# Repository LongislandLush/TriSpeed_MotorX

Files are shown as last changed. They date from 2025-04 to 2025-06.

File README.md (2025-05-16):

# TriSpeed_MotorX
STM32-based 3-speed DC motor controller with PWM, UART, and state logic

TriSpeed MotorX 是一個基於 STM32 Nucleo-F446RE 開發板的小型馬達控制專案，
實現了按鈕切換三段轉速、OLED即時顯示當前狀態，並透過 UART 通訊將速度資訊同步給 Arduino，控制 RGB LED 顏色變化。





# 系統架構
## STM32 X Arduino X UART X PWM X OLED 系統架構圖
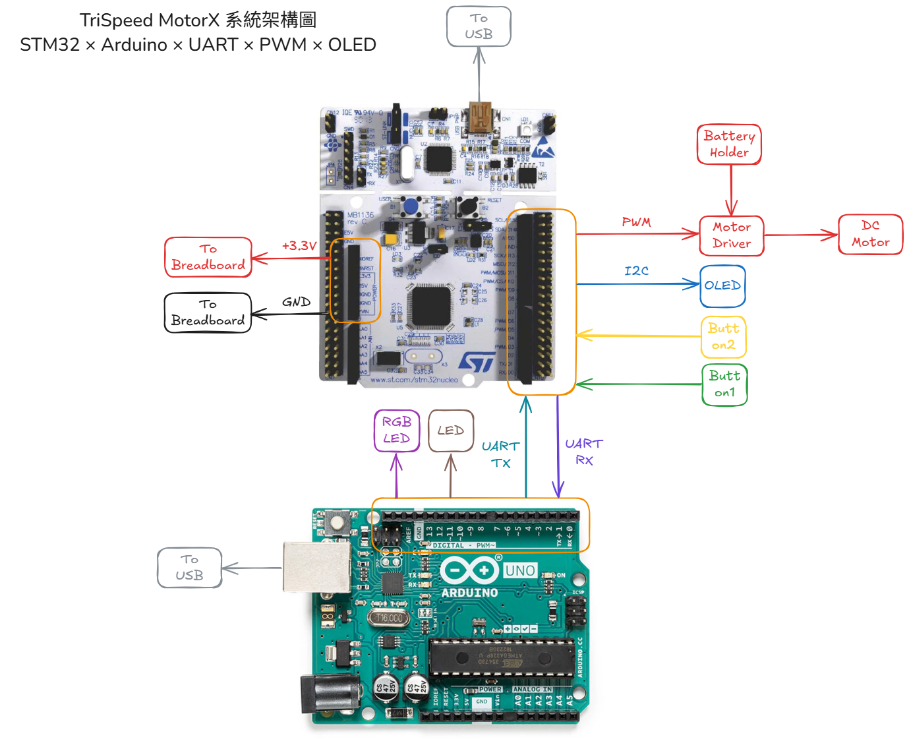
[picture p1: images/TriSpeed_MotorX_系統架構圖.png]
TriSpeed_MotorX_系統架構圖


## Normal Mode 流程圖
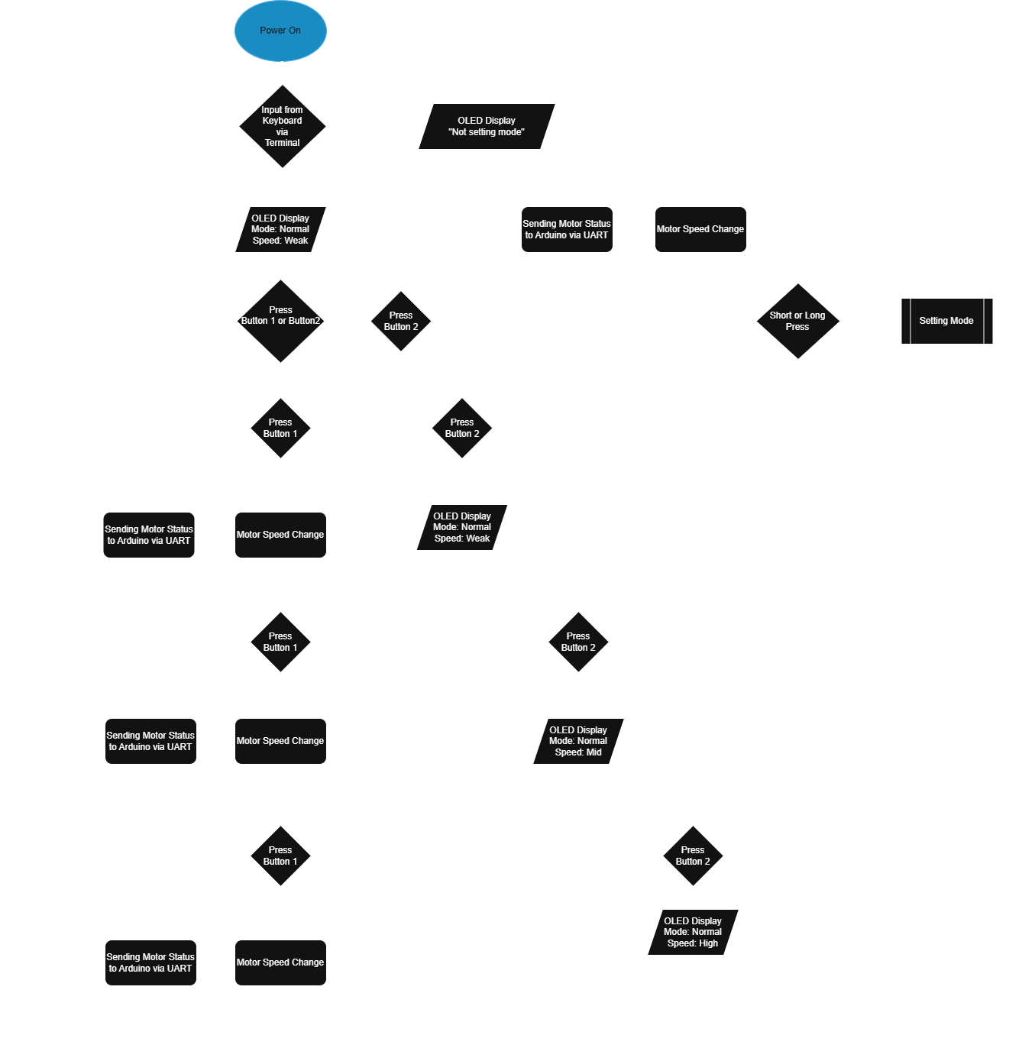
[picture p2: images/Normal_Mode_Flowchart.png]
Normal Mode Flowchart


## Setting Mode 流程圖
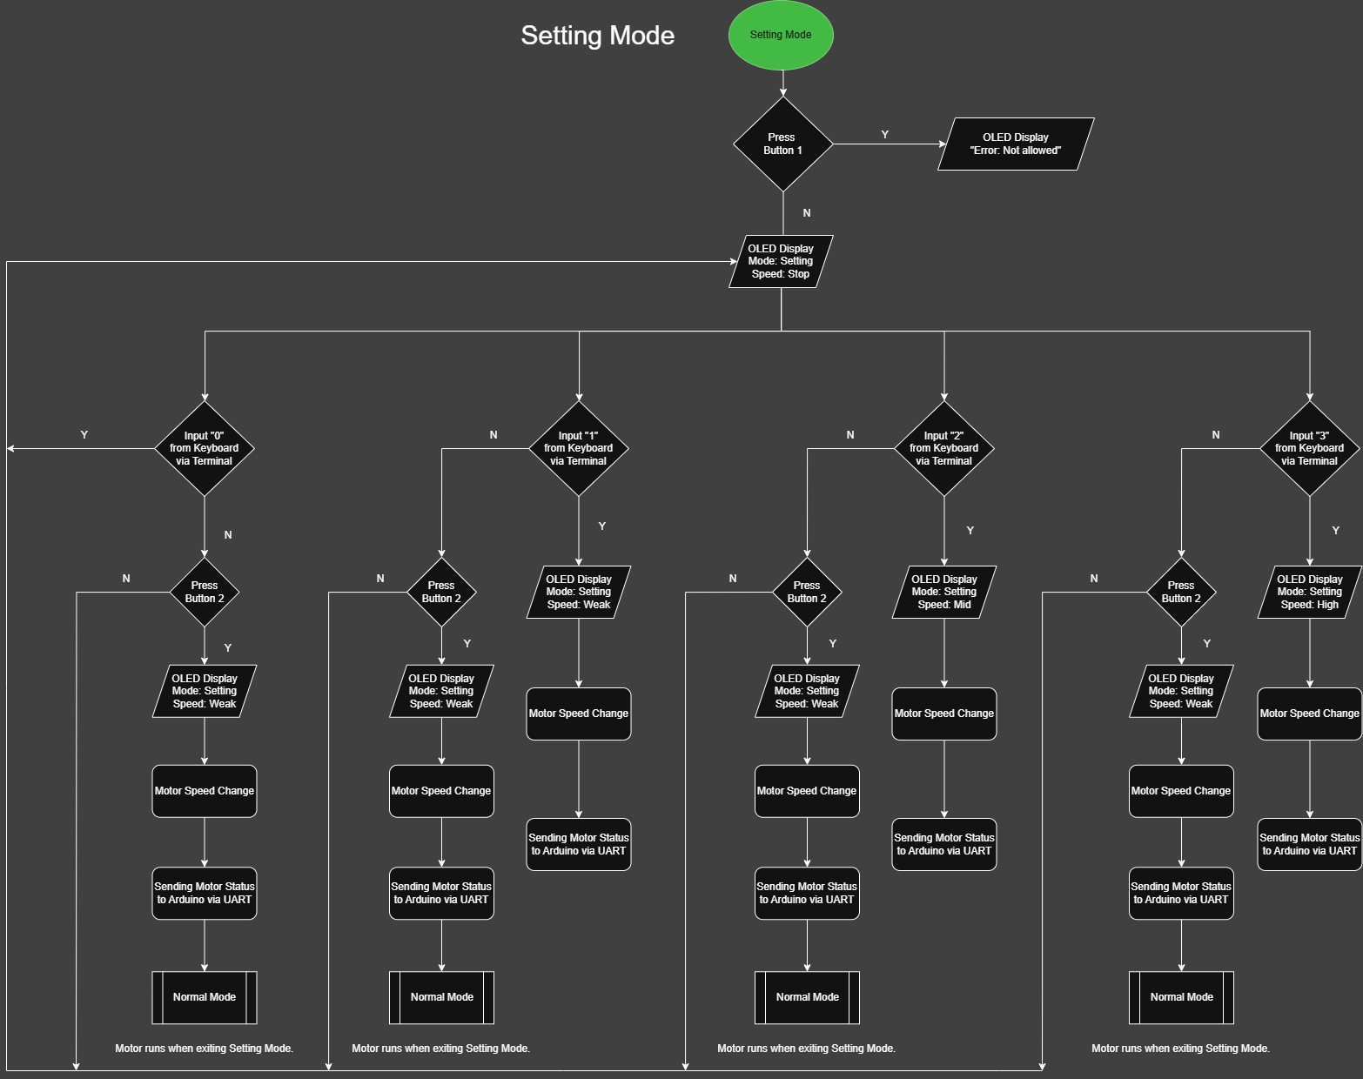
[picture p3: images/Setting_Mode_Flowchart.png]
Setting Mode Flowchart


# 使用方式

環境準備
1. 開啟 STM32CubeIDE
參考 STM32/ 資料夾內的 main.c 與 .ioc 設定，燒錄至 Nucleo-F446RE 開發板。

2. 開啟 Arduino IDE
參考 Arduino/ 資料夾內的 .ino 檔案，燒錄至 Arduino Uno R3。

3. 接線參考
請依據 images/ 資料夾內的接線圖進行連接，特別注意以下幾點：

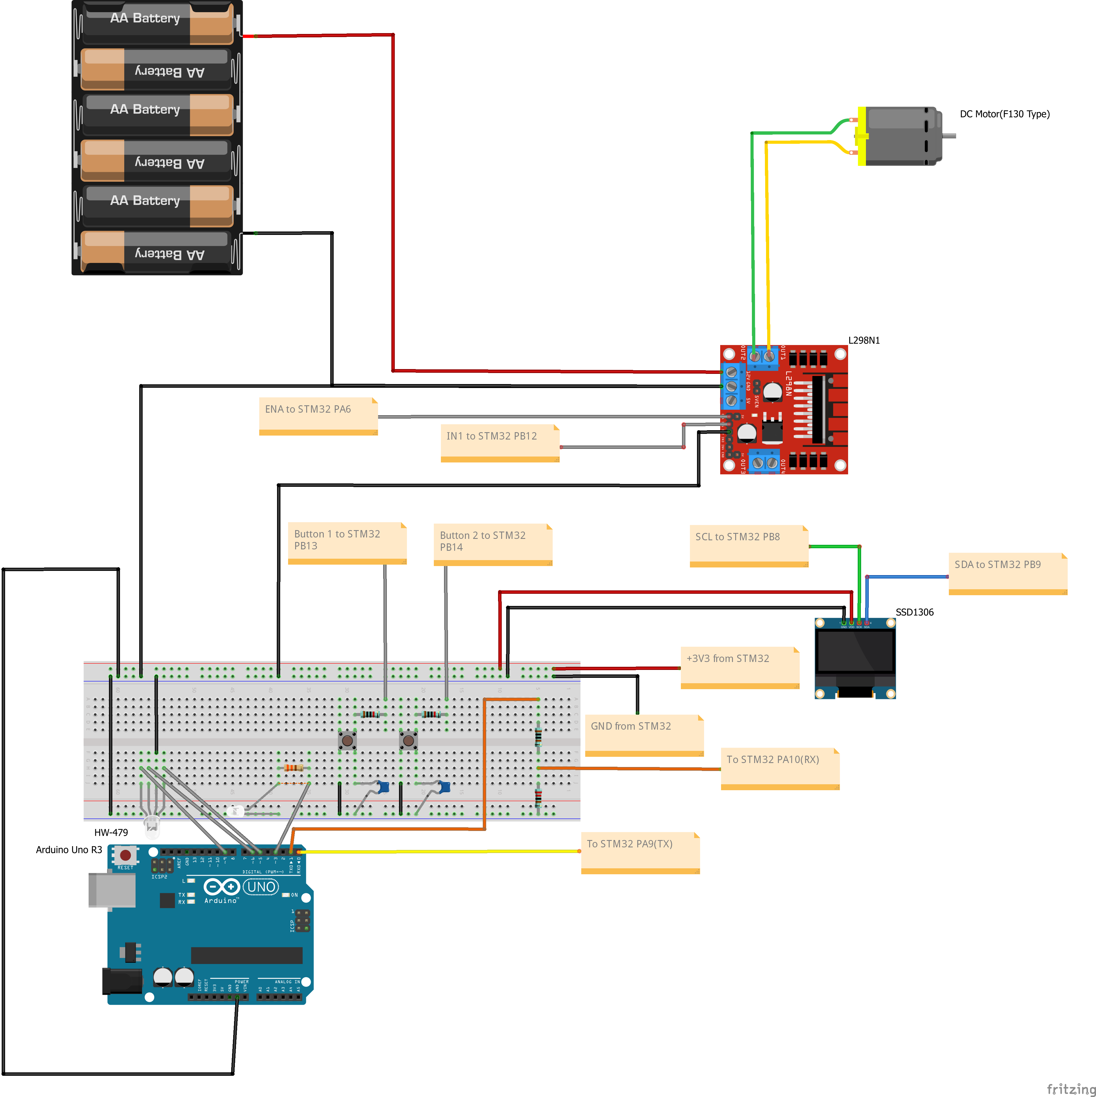
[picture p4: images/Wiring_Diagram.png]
Wiring Diagram


注意事項
1. STM32 使用 +3.3V，Arduino 為 +5V, 
STM32 TX 可直接接 Arduino RX, 
Arduino TX 請透過電阻分壓後再接 STM32 RX（避免超壓損壞）

2. L298N 馬達模組使用 6 顆 AA 電池獨立供電, 
電池盒負極、模組負極、STM32 和 Arduino 皆需「共地」

3. 按鈕設有防彈跳電路，LED 有限流電阻, 
詳細接線請參見 images/ 接線圖

測試流程建議

1. 確認接線無誤並燒錄韌體

2. 按鈕1 測試三段速度循環是否正確

3. 按鈕2 測試 Reset 功能與Setting Mode切換

4. 使用 UART 終端機測試Setting Mode下的數字指令（0~3）

5. 確認 OLED 顯示與 RGB 燈變化與馬達一致

# 功能說明

1. 三段轉速切換（弱、中、強）=> 按鈕1：短按依序切換 弱 ➔ 中 ➔ 強

2. Reset 與 Setting Mode => 按鈕2：短按重設為弱速、長按進入設定模式（馬達停止）

3. 設定模式 UART 控制 => Setting下，可透過 UART 傳送數字指令 (0, 1, 2, 3) 切換馬達轉速

4. OLED 顯示 => 顯示目前模式（Normal / Setting）與轉速狀態（Stop / Weak / Mid / High）

5. UART 傳送至 Arduino 控制 RGB LED => 將目前狀態傳送至 Arduino，控制 RGB 燈顏色變化

# 使用技術與工具

**IDE**: 

1. STM32CubeIDE
   
2. Arduino IDE

**Hardware**: 

1. STM32F446RE Nucleo Board x1
 
2. Arduino Uno x1
 
3. OLED (SSD1306) x1
 
4. L298N Motor Driver Module x1
 
5. DC Motor(F130 Type) x1
 
6. RGB LED Module(HW-479) x1
 
7. LED(White) x1
 
8. Push Button x2
 
9. 6xAA Battery Holder x1

10. Resistors:
    – 330 Ω ×1
    – 1 kΩ ×1
    – 2 kΩ ×1
    – 10 kΩ ×2

11. Capacitors:
    – 104 Ceramic Capacitor (0.1 µF) ×2

12. Breadboard ×1

13. Jumper Wires: Male-to-Male, Male-to-Female (Depending on connection)

**Software**:

1. Realterm

**Knowledge:**

1. PWM 控制直流馬達轉速
   
2. 按鈕消除彈跳
 
3. UART通訊
 
4. C Programming Language

# 開發過程重點

1. 實作軟體與電路層級的去彈跳機制，有效避免按鈕誤觸。

2. 導入狀態機（State Machine）架構，實現模式與速度的穩定切換。

3. 透過分壓電路解決不同開發板間 UART 通訊的電壓相容問題。

4. 使用 OLED 即時顯示當前模式與馬達狀態，並可透過終端機進行遠端操作與控制。

***所有零件皆為常見開發模組，適合初學者搭建與測試***

# 成果展示

點擊下方觀看實際操作影片，展示三段轉速切換、OLED 顯示與 UART 控制 RGB LED：

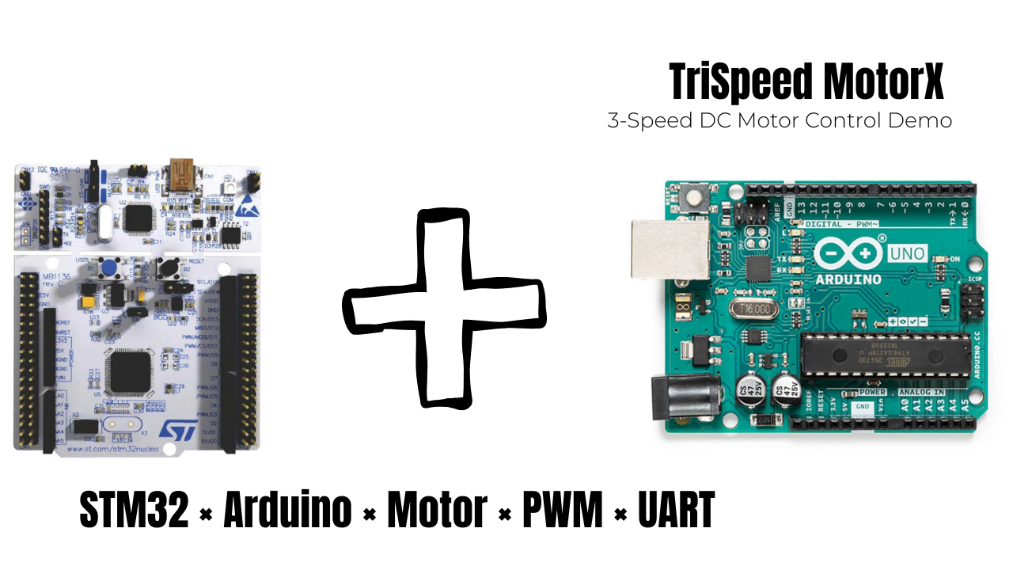
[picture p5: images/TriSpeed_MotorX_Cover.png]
TriSpeed MotorX Demo (https://youtu.be/fkt2jXf6d6g)


> 實體操作按鈕切換弱 / 中 / 強速  
> OLED 即時顯示控制模式與速度狀態  
> RGB LED 隨 UART 指令變色同步展示

實體接線圖
實體照

### Issues Resolved

1. **Reset does not restore breathing light in setting mode**  
**Description:**  
Pressing the reset button on the STM32 board while in setting mode would leave the Arduino in an incorrect LED state (e.g., flashing white or purple instead of the default warm-colored breathing light).

**Fix:**  
Sent UART commands `'e'` and `'0'` during STM32 startup to force the Arduino to exit setting mode and restore the default speed level (0).

2. **Speed level 3 occasionally drops to level 1**  
**Description:**  
In both Normal Mode and Setting Mode, high speed mode (level 3) would occasionally revert to low speed (level 1).  
The issue was caused by EMI generated from motor current, which affected the BTN2 GPIO logic — leading to false trigger detection.

**Fix:**  
1. Investigated both EXTI interrupt and polling-based logic for BTN2 handling. Both approaches can be stable if hardware EMI is controlled properly.  
2. Physically isolated the STM32 and L298N modules from the conductive metal base using an anti-static bag, preventing ground loop interference and suppressing EMI-induced behavior.

**Verification:**  
- With anti-static insulation: both interrupt and polling methods passed 2–3 minute stress tests under high-speed mode  
- Without insulation: polling mode consistently exhibited instability, confirming that the core issue was hardware-induced

# 授權
***本專案以 MIT License 授權開源使用。***

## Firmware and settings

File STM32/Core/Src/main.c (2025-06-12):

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
/* Includes ------------------------------------------------------------------*/
#include "main.h"

/* USER CODE BEGIN Includes */

#include <stdio.h>   // For sprintf
#include <string.h>  // For strlen
#include <stdarg.h>

#include "ssd1306.h" // From GitHub https://github.com/afiskon/stm32-ssd1306
#include "ssd1306_fonts.h" // From GitHub https://github.com/afiskon/stm32-ssd1306

/* USER CODE END Includes */

I2C_HandleTypeDef hi2c1;

TIM_HandleTypeDef htim3;

UART_HandleTypeDef huart1;
UART_HandleTypeDef huart2;

/* USER CODE BEGIN PV */

/*上面註解每次Generate Code都會被清掉移來這裡
 * 開啟I2C, Timer3, UART1
 * 另外UART2是建專案就開起的*/

/* USER CODE BEGIN PV */

volatile uint8_t btn2_down = 0;       //按鍵是否正在被按下（由中斷設為 1，放開時重設為 0）
volatile uint8_t btn2_released = 0;   //是否已經放開按鍵（偵測到釋放後設為 1，處理完後清除）
volatile uint32_t btn2_press_time = 0;//BTN2 按下當下的時間（用於計算按住時間以區分長按／短按）
volatile uint32_t btn2_release_debounce_time = 0;//放開時的防彈跳時間（確保放開維持一段時間才觸發事件）

// Motor state
volatile uint8_t speed_level = 0; //當前馬達轉速等級（0=停止, 1~3 對應弱/中/強）
volatile uint8_t uart_override = 0; //是否由 UART 控制速度（1=UART 控制, 0=按鈕控制）

// Button state
volatile uint8_t config_mode = 0; //是否進入設定模式（1=Config 模式, 只能用 UART 控制）
volatile uint8_t flag_btn1_pressed = 0; //BTN1 中斷觸發後設為 1，主程式內會依此切換速度，處理完後清除
volatile uint8_t flag_btn2_pressed = 0; //保留：目前未使用，可作為 BTN2 事件觸發用
volatile uint32_t last_btn1_time = 0; //BTN1 上次觸發時間（防彈跳用）
volatile uint32_t last_btn2_time = 0; //BTN2 上次觸發時間（防彈跳用）
uint32_t press_time = 0; //非 volatile，暫存按下時間（可與 BTN2 共用）

// UART RX
uint8_t rx_data; //USART2 單位元接收暫存區（配合 UART 中斷）

//Error Message
char oled_msg[22] = "";  //OLED 顯示訊息（最多 21 字元 + 1 個結尾 '\0'）
uint32_t oled_msg_time = 0; //訊息顯示起始時間（2 秒後自動清除）


/* USER CODE END PV */

void SystemClock_Config(void);
static void MX_GPIO_Init(void);
static void MX_USART2_UART_Init(void);
static void MX_TIM3_Init(void);
static void MX_I2C1_Init(void);
static void MX_USART1_UART_Init(void);
/* USER CODE BEGIN PFP */

/* --------------------------------------------------------------------------
 * 自己添加的私有函式宣告區（Private Function Prototypes）
 * 用於 OLED 顯示、錯誤訊息更新等自訂功能
 * -------------------------------------------------------------------------- */

void update_oled_display(void); //更新 OLED 顯示內容（狀態 / 轉速）
void oled_message(const char* fmt, ...);  //顯示錯誤訊息（支援格式化輸入


/* USER CODE END PFP */

/* USER CODE BEGIN 0 */

/*設定馬達轉速並根據狀態傳送對應 RGB 指令給 Arduino
 * mode 馬達速度等級（0=停止, 1=弱速, 2=中速, 3=高速）
 * 對應 PWM duty 為 0%, 20%, 50%, 80%
 */

void set_motor_speed(uint8_t mode)
{
    uint32_t duty = 0; //用於設定 PWM 輸出佔空比
    char rgb_cmd = '0';  //要透過 UART 傳送給 Arduino 的 RGB 控制（預設為 0：呼吸燈）
    //根據 mode 設定 PWM duty 與對應 RGB 指令
    switch(mode)
    {
        case 1: duty = 20; rgb_cmd = '1'; break; //弱速：20%，綠色系燈號
        case 2: duty = 50; rgb_cmd = '2'; break; //中速：50%，橙黃色系燈號
        case 3: duty = 80; rgb_cmd = '3'; break; //高速：80%，紅色系燈號
        default: duty = 0; rgb_cmd = '0'; break; //停止：0%，暖色系呼吸燈（待機）
    }
    //更新PWM的duty,控制馬達轉速
    __HAL_TIM_SET_COMPARE(&htim3, TIM_CHANNEL_1, duty);

    //僅在非設定模式下，主動透過 UART 傳送燈號控制指令給 Arduino（若為設定模式，應由使用者手動下指令控制燈色）
    if (!config_mode) {
        HAL_UART_Transmit(&huart1, (uint8_t *)&rgb_cmd, 1, HAL_MAX_DELAY);
    }

    //將變更結果印出到 UART2，可透過 PC 端 terminal 觀察（如 TeraTerm、PuTTY、RealTerm）
    printf("Speed changed to: %d\r\n", mode);
}



/* 開機時於 UART2 顯示控制說明
 * 包含：按鈕功能說明、UART 可輸入的控制指令格式等。
 * 可搭配 PC 端 terminal（TeraTerm / PuTTY / RealTerm）查看。
 */
void print_banner() {
    printf("=== TriSpeed MotorX v1.0 ===\r\n");
    printf("BTN1: PB13 - speed cycle\r\n");
    printf("BTN2: PB14 - short=reset, long=stop\r\n");
    printf("UART: 1/2/3/0=set, x=release override\r\n\r\n");
}

/* USER CODE END 0 */

/**
  * @brief  The application entry point.
  * @retval int
  */
int main(void)
{

  /* MCU Configuration--------------------------------------------------------*/

  /* Reset of all peripherals, Initializes the Flash interface and the Systick. */
  HAL_Init();

  /* Configure the system clock */
  SystemClock_Config();

  /* Initialize all configured peripherals */
  MX_GPIO_Init();
  MX_USART2_UART_Init();
  MX_TIM3_Init();
  MX_I2C1_Init();
  MX_USART1_UART_Init();
  /* USER CODE BEGIN 2 */

  //OLED 初始化與清除畫面
  ssd1306_Init(); //初始化 SSD1306 模組
  ssd1306_Fill(Black); //清除畫面
  ssd1306_UpdateScreen(); //將內容更新至 OLED

  /* USER CODE BEGIN 2 */

  //啟動外設功能
  HAL_TIM_PWM_Start(&htim3, TIM_CHANNEL_1);  //啟動馬達 PWM 控制
  HAL_UART_Receive_IT(&huart2, (uint8_t *)&rx_data, 1);   //啟動 UART2 非阻塞接收（PC端指令）

  //預設值：上電後為 Normal Mode（config_mode = 0）且馬達停止（speed_level = 0）
  config_mode = 0;
  speed_level = 0;  //speed_level = 0 對應「停止 + 呼吸燈」

  //---------- 通知 Arduino 離開設定模式 ----------
  //原本問題：若未主動通知，Arduino 仍保留在設定模式，導致顯示錯誤燈號（如閃爍白燈或藍紫燈）
  //解法：主動送出 'e'，代表退出設定模式（exit）
  char rgb_cmd_exit = 'e';
  HAL_UART_Transmit(&huart1, (uint8_t *)&rgb_cmd_exit, 1, HAL_MAX_DELAY);

  HAL_Delay(100);  //延遲一小段時間，確保 Arduino Serial 有足夠時間完成初始化

  //---------- 傳送預設燈號狀態 ----------
  //speed_level = 0 對應預設燈號（呼吸燈），需傳送 '0' 給 Arduino
  char rgb_cmd_mode = '0';
  HAL_UART_Transmit(&huart1, (uint8_t *)&rgb_cmd_mode, 1, HAL_MAX_DELAY);

  //系統初始狀態處理
  print_banner(); //列印操作說明，建議搭配 PC 端 terminal 使用（TeraTerm / PuTTY / RealTerm）
  set_motor_speed(speed_level); //設定初始速度（預設為 0：停止）
  update_oled_display(); //顯示初始狀態至 OLED

  //BTN2 釋放 debounce 時間初始化（延遲觸發防彈跳）
  static uint32_t btn2_release_debounce_time = 0;

  //拉高馬達 IN1 腳位(接在L298N模組)，固定馬達旋轉方向(只控制一個方向)
  HAL_GPIO_WritePin(GPIOB, GPIO_PIN_12, GPIO_PIN_SET);

  /* USER CODE END 2 */

  /* Infinite loop */
  /* USER CODE BEGIN WHILE */
  while (1)
  {

	  	  //---------- BTN1 被按下的處理邏輯 ----------
	      if (flag_btn1_pressed)
	      {
	          if (!config_mode)
	          {

	        	  //Normal 模式中循環切換速度（1 → 2 → 3 → 1）
	              speed_level++;
	              if (speed_level > 3) speed_level = 1;
	              set_motor_speed(speed_level);
	              printf("[BTN1] Speed -> %d (Normal Mode)\r\n",speed_level);
	          }
	          else
	          {

	        	  //設定模式中不允許按 BTN1 切換速度
	        	  printf("[BTN1] Invalid: In setting mode. Use UART.\r\n");
	        	  oled_message("Error: Not allowed");

	              flag_btn1_pressed = 0; //清除事件旗標

	              continue;//跳過更新，重新跑 while-loop

	          }

	          update_oled_display(); //顯示當前速度
	          flag_btn1_pressed = 0; //清除事件旗標
	      }

	      //---------- BTN2 輪詢（已停用，備用作為中斷替代方案） ----------
	      /*
	      if (!btn2_down && HAL_GPIO_ReadPin(GPIOB, GPIO_PIN_14) == GPIO_PIN_RESET)
	      {
	          btn2_down = 1;
	          btn2_press_time = HAL_GetTick();
	          btn2_release_debounce_time = 0; //初始化釋放計時器
	      }

	      //持續輪詢偵測放開動作（需維持高電位超過 100ms 才視為放開）
		  if (btn2_down && HAL_GPIO_ReadPin(GPIOB, GPIO_PIN_14) == GPIO_PIN_SET)
		  {
			  //第一次偵測放開 → 開始計時
			  if (btn2_release_debounce_time == 0)
				  btn2_release_debounce_time = HAL_GetTick();

			  //放開狀態維持超過 100ms → 視為正式放開
			  if (HAL_GetTick() - btn2_release_debounce_time > 100)
			  {
				  btn2_down = 0;
				  btn2_released = 1;
				  btn2_release_debounce_time = 0; //重設

				  uint32_t press_duration = HAL_GetTick() - btn2_press_time;

				  if (press_duration < 1000)
				  {

					  //短按處理：重設為弱速 + 離開設定模式
					  speed_level = 1;
					  config_mode = 0;
					  printf("[BTN2] Short Press: Reset to weak speed. Exit setting mode.\r\n");

					  //通知 Arduino 離開設定模式（'e'）
					  char rgb_cmd = 'e';
					  HAL_UART_Transmit(&huart1, (uint8_t *)&rgb_cmd, 1, HAL_MAX_DELAY);
				  }
				  else
				  {

					  //長按處理：進入設定模式 + 馬達停止
					 speed_level = 0;
					 config_mode = 1;
					 printf("[BTN2] Long Press: Enter setting mode. Motor stopped.\r\n");

					 set_motor_speed(speed_level);  //停止馬達
					 update_oled_display(); //顯示 "Mode: Setting"

					 //通知 Arduino 進入設定模式（'s'）
					 char rgb_cmd = 's';
					 HAL_UART_Transmit(&huart1, (uint8_t *)&rgb_cmd, 1, HAL_MAX_DELAY);

				  }

				  //最後統一更新顯示與速度
				  set_motor_speed(speed_level);
				  update_oled_display();

			  }
		  }

		  else
		  {
			  //若尚未穩定放開（bounce or 持續按壓）→ 重設釋放計時器
			  btn2_release_debounce_time = 0;
		  } */

	      //---------- BTN2 放開偵測（中斷版本用） ----------
	      if (btn2_down && HAL_GPIO_ReadPin(GPIOB, GPIO_PIN_14) == GPIO_PIN_SET)
	      {
	    	  //第一次偵測放開 → 開始計時
	    	  if (btn2_release_debounce_time == 0)
	              btn2_release_debounce_time = HAL_GetTick();

	          //放開狀態維持超過 100ms → 視為正式放開
	          if (HAL_GetTick() - btn2_release_debounce_time > 100)
	          {
	              btn2_down = 0;
	              btn2_released = 1;
	              printf("[EXTI] BTN2 released after %lu ms\r\n", HAL_GetTick() - btn2_press_time);
	              btn2_release_debounce_time = 0; //重設
	          }
	      }

		  else
		  {
			  //仍然按著 or 彈跳中 → 放開計時重置
			  btn2_release_debounce_time = 0;
		  }

	      //---------- BTN2 放開後的處理邏輯 ----------
	      if (btn2_released)
	      {

	    	  btn2_released = 0;

	          uint32_t press_duration = HAL_GetTick() - btn2_press_time;

	          if (press_duration < 1000)
	          {

	        	  //短按 → 重設為弱速、離開設定模式
	        	  speed_level = 1;
				  config_mode = 0;
				  printf("[BTN2] Short Press: Reset to weak speed. Exit setting mode.\r\n");

				  //通知 Arduino 離開設定模式（'e'）
				  char rgb_cmd = 'e';
				  HAL_UART_Transmit(&huart1, (uint8_t *)&rgb_cmd, 1, HAL_MAX_DELAY);
	          }
	          else
	          {

	        	 //長按 → 停止馬達並進入設定模式
	        	 speed_level = 0;
				 config_mode = 1;
				 printf("[BTN2] Long Press: Enter setting mode. Motor stopped.\r\n");

				 set_motor_speed(speed_level);  //停止馬達
				 update_oled_display(); //顯示 "Mode: Setting"

				 //通知 Arduino 進入設定模式（'s'）
				 char rgb_cmd = 's';
				 HAL_UART_Transmit(&huart1, (uint8_t *)&rgb_cmd, 1, HAL_MAX_DELAY);

	          }

	          //統一更新顯示與馬達狀態
	          set_motor_speed(speed_level);
	          update_oled_display();

	      }

    /* USER CODE END WHILE */

    /* USER CODE BEGIN 3 */
  }
  /* USER CODE END 3 */
}

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
/* USER CODE BEGIN 4 */

/* 外部中斷回呼函式，用來處理 BTN1（PB13）與 BTN2（PB14）按下事件
 *
 * 僅在中斷觸發時紀錄按下時間或設定事件旗標，避免在中斷中執行繁重邏輯。
 * BTN1：速度切換（設定 flag）
 * BTN2：判斷長按/短按（記錄按下時間，放開由主迴圈偵測）
 */

void HAL_GPIO_EXTI_Callback(uint16_t GPIO_Pin)
{
    uint32_t now = HAL_GetTick();  //取得目前時間（單位：ms）

    //---------- BTN1（PB13）按下事件 ----------
    if (GPIO_Pin == GPIO_PIN_13)
    {

    	if(config_mode) //設定模式下，直接略過 BTN1 中斷處理
    		return;

    	//若距離上次觸發已超過 150ms → 防彈跳
    	if (now - last_btn1_time > 150)  //防彈跳間隔 150ms
        {

    		if (HAL_GPIO_ReadPin(GPIOB, GPIO_PIN_13) == GPIO_PIN_RESET){

    			flag_btn1_pressed = 1; //設定旗標，主程式會依此處理速度切換

    			last_btn1_time = now; //更新上次觸發時間

    		}
        }
    }

    //---------- BTN2（PB14）按下事件 ----------
    //註：曾懷疑 speed_level = 3 自動跳回 1 是因馬達 EMI 誤觸中斷所致
    else if (GPIO_Pin == GPIO_PIN_14)
    {
    	 //若距離上次觸發已超過 150ms → 防彈跳
    	if (now - last_btn2_time > 150)
        {
            last_btn2_time = now;

            //確保不是連續觸發，並再次確認當下電平為低（按下狀態）
			if (!btn2_down && HAL_GPIO_ReadPin(GPIOB, GPIO_PIN_14) == GPIO_PIN_RESET)  //加強判斷
            {
            	btn2_down = 1; //標記為正在按住狀態
                btn2_press_time = now; //記錄按下時間（用於判斷長按 or 短按）
                btn2_release_debounce_time = 0; //初始化放開 debounce 計時
                printf("[EXTI] BTN2 pressed at %lu ms\r\n", now);
            }
        }
    }
}


/* 接收完成中斷回呼函式
 *
 * 當 USART2 接收到 1 個 byte 資料後觸發。僅在進入 Config Mode（設定模式）時允許透過 UART 改變馬達轉速。
 * 否則會拒絕並顯示錯誤訊息。
 */

void HAL_UART_RxCpltCallback(UART_HandleTypeDef *huart)
{
	//確認此次中斷是來自 USART2（從PC端Terminal傳來的資料）
	if (huart->Instance == USART2)
    {
        uint8_t new_speed = speed_level; //預設為目前速度，後續判斷是否需要變更

        if (config_mode) //僅在設定模式下允許 UART 控速
        {
            switch(rx_data)
            {
                case '1': new_speed = 1; break;
                case '2': new_speed = 2; break;
                case '3': new_speed = 3; break;
                case '0': new_speed = 0; break;

                //非法輸入：顯示錯誤訊息至 Terminal + OLED
                default:
                	printf("[UART ] Invalid input: %c\r\n", rx_data);
                	oled_message("Invalid input: %c", rx_data);
                	break;

            }


            //若有變更速度，則更新 PWM、OLED 與 Arduino RGB
            if (new_speed != speed_level) {

            	speed_level = new_speed; //更新馬達速度

                set_motor_speed(speed_level); //變更 PWM 輸出

                update_oled_display(); //OLED 顯示當前狀態

                //將原始輸入字元透過 UART 傳送給 Arduino，控制 RGB 燈色
                char rgb_cmd = rx_data; // '1', '2', '3', '0'

                HAL_UART_Transmit(&huart1, (uint8_t *)&rgb_cmd, 1, HAL_MAX_DELAY);

                printf("[UART ] Speed -> %d (Setting Mode)\r\n", speed_level);
            }
        }

        else //非設定模式 → 拒絕 UART 控制
        {
            printf("[UART ] Ignored: Not in setting mode. Long press BTN2 to enable.\r\n");

            oled_message("Not setting mode"); //顯示錯誤訊息至 OLED

            update_oled_display();  //刷新 OLED 畫面（有錯誤提示）
        }

        //重新啟用 UART 接收中斷（非一次性，要持續接收）
        HAL_UART_Receive_IT(&huart2, &rx_data, 1);
    }
}

/* 更新 OLED 顯示內容
 *
 * 顯示專案標題、當前模式（Normal / Setting）、速度狀態（Weak / Mid / High / Stop），
 * 並在有錯誤訊息時顯示提示，超過 2 秒自動清除。
 */

void update_oled_display(void)
{
    ssd1306_Fill(Black); //清空螢幕（塗滿黑色背景）

    //顯示標題：TriSpeed MotorX
    ssd1306_SetCursor(0, 0);
    ssd1306_WriteString("TriSpeed MotorX", Font_7x10, White);

    //顯示目前模式（設定模式或一般模式）
    ssd1306_SetCursor(0, 16);
    if (config_mode)
        ssd1306_WriteString("Mode: Setting", Font_7x10, White); //設定模式
    else
        ssd1306_WriteString("Mode: Normal", Font_7x10, White); //設定模式

    //顯示目前速度狀態
    ssd1306_SetCursor(0, 32);
    switch (speed_level)
    {
    	case 0: ssd1306_WriteString("Speed: Stop", Font_7x10, White); break;
        case 1: ssd1306_WriteString("Speed: Weak", Font_7x10, White); break;
        case 2: ssd1306_WriteString("Speed: Mid", Font_7x10, White); break;
        case 3: ssd1306_WriteString("Speed: High", Font_7x10, White); break;
    }

    //顯示錯誤訊息（如有），最多顯示 2 秒
    ssd1306_SetCursor(0, 48);
        if (oled_msg[0] != '\0' && HAL_GetTick() - oled_msg_time < 2000) {
            ssd1306_WriteString(oled_msg, Font_7x10, White); //顯示訊息
        } else {
            oled_msg[0] = '\0';  //時間到 → 自動清除內容
        }

    ssd1306_UpdateScreen(); //最後統一更新畫面（送出到 OLED）
}

/*顯示格式化錯誤訊息至 OLED，並記錄出現時間（維持顯示 2 秒）
*
* 此函式支援 printf-style 格式化文字，例如：
* oled_message("Invalid input: %c", rx_data);
*
* 實際顯示與時間控制交由 update_oled_display() 處理。
*
* fmt 欲顯示的格式化字串（支援 %d、%c、%s 等格式）
*/

void oled_message(const char* fmt, ...) {
    va_list args; //宣告可變參數清單
    va_start(args, fmt); //初始化參數讀取（從 fmt 開始）
    vsnprintf(oled_msg, sizeof(oled_msg), fmt, args); //將格式化後的字串寫入 oled_msg[]
    va_end(args); //結束參數讀取
    oled_msg_time = HAL_GetTick(); //記錄目前時間，用於後續計算是否超過顯示時間
}


#ifdef __GNUC__
#define PUTCHAR_PROTOTYPE int __io_putchar(int ch) //GCC 編譯器預設的 printf 輸出函式
#else
#define PUTCHAR_PROTOTYPE int fputc(int ch, FILE *f) //其他編譯器（如 KEIL）預設用 fputc
#endif

//將 printf 的輸出字元透過 UART2 傳送出去
PUTCHAR_PROTOTYPE
{
    HAL_UART_Transmit(&huart2, (uint8_t *)&ch, 1, HAL_MAX_DELAY); //實際傳送字元給電腦端
    return ch; //回傳該字元，讓 printf 繼續下一個字元
}

/* USER CODE END 4 */
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


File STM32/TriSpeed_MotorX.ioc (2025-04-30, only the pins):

Mcu.UserName=STM32F446RETx
PA10.Signal=USART1_RX
PA13.GPIO_Label=TMS
PA13.Signal=SYS_JTMS-SWDIO
PA14.GPIO_Label=TCK
PA14.Signal=SYS_JTCK-SWCLK
PA2.GPIO_Label=USART_TX
PA2.Signal=USART2_TX
PA3.GPIO_Label=USART_RX
PA3.Signal=USART2_RX
PA5.GPIO_Label=LD2 [Green Led]
PA5.Signal=GPIO_Output
PA6.Signal=S_TIM3_CH1
PA9.Signal=USART1_TX
PB12.GPIO_Label=Motor_IN1
PB12.Signal=GPIO_Output
PB13.GPIO_Label=Switch1
PB13.Signal=GPXTI13
PB14.GPIO_Label=Switch2
PB14.Signal=GPXTI14
PB3.GPIO_Label=SWO
PB3.Signal=SYS_JTDO-SWO
PB8.Signal=I2C1_SCL
PB9.Signal=I2C1_SDA
PC14-OSC32_IN.Signal=RCC_OSC32_IN
PC15-OSC32_OUT.Signal=RCC_OSC32_OUT
PH0-OSC_IN.Signal=RCC_OSC_IN
PH1-OSC_OUT.Signal=RCC_OSC_OUT

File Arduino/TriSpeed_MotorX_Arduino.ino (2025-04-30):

#define RED_PIN     5
#define GREEN_PIN   6
#define BLUE_PIN    9
#define WHITE_PIN   3
//#define BTN1_PIN    7

bool settingMode = false;
int speedMode = 0;  // 0=呼吸、1=綠、2=黃、3=紅

void setup() {
  pinMode(RED_PIN, OUTPUT);
  pinMode(GREEN_PIN, OUTPUT);
  pinMode(BLUE_PIN, OUTPUT);
  pinMode(WHITE_PIN, OUTPUT);
  //pinMode(BTN1_PIN, INPUT_PULLUP);

  Serial.begin(115200);
}

void loop() {
  handleSerial();
  //handleButton();

  if (settingMode) {
    blinkWhiteLED();
    showSettingRGB();
  } else {
    digitalWrite(WHITE_PIN, LOW);
    showNormalRGB();
  }
}

void handleSerial() {
  if (Serial.available()) {
    char ch = Serial.read();
    if (ch == 's') {
      settingMode = true;
      speedMode = 0;
    } else if (ch == 'e') {
      settingMode = false;
    } else if (ch >= '0' && ch <= '3') {
      speedMode = ch - '0';
    }
  }
}

/*void handleButton() {
  static unsigned long lastBtnTime = 0;
  if (!settingMode && digitalRead(BTN1_PIN) == LOW) {
    if (millis() - lastBtnTime > 300) {
      speedMode++;
      if (speedMode > 3) speedMode = 0;
      lastBtnTime = millis();
    }
  }
}*/

void blinkWhiteLED() {
  static unsigned long lastToggle = 0;
  static bool ledState = false;
  if (millis() - lastToggle > 500) {
    ledState = !ledState;
    digitalWrite(WHITE_PIN, ledState);
    lastToggle = millis();
  }
}

void showNormalRGB() {
  switch (speedMode) {
    case 0: warmBreathing(); break;
    case 1: rgb(0, 255, 0); break;      // 綠
    case 2: rgb(255, 255, 0); break;    // 黃
    case 3: rgb(255, 0, 0); break;      // 紅
  }
}

void showSettingRGB() {
  static unsigned long lastToggle = 0;
  static bool flashState = false;
  static int breath = 0;
  static int delta = 2;

  if (speedMode == 0) {
    if (millis() - lastToggle > 15) {
      breath += delta;
      if (breath > 255 || breath < 0) delta = -delta;
      breath = constrain(breath, 0, 255);
      rgb(breath / 2, 0, breath);  // 藍紫呼吸燈
      lastToggle = millis();
    }
  } else {
    if (millis() - lastToggle > 300) {
      flashState = !flashState;
      lastToggle = millis();
    }
    if (flashState) {
      switch (speedMode) {
        case 1: rgb(0, 255, 0); break;
        case 2: rgb(255, 255, 0); break;
        case 3: rgb(255, 0, 0); break;
      }
    } else {
      rgb(0, 0, 0);
    }
  }
}

void warmBreathing() {
  static unsigned long lastTime = 0;
  static int b = 0;
  static int delta = 2;

  if (millis() - lastTime > 15) {
    b += delta;
    if (b > 255 || b < 0) delta = -delta;
    b = constrain(b, 0, 255);
    rgb(b, b / 4, 0);  // 橘紅呼吸
    lastTime = millis();
  }
}

void rgb(int r, int g, int b) {
  analogWrite(RED_PIN, r);
  analogWrite(GREEN_PIN, g);
  analogWrite(BLUE_PIN, b);
}

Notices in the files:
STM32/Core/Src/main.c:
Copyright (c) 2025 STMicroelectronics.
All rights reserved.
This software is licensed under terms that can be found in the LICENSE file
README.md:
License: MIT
